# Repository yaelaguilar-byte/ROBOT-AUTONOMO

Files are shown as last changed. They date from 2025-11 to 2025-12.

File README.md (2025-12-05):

Introduction and description of the project: This project is a proposal for an Autonomous Robot, developed from modifications made to a radio-controlled (RC) car chassis obtained from a content creator known as ""Duke Doks" through his YouTube channel and his official website:

https://dukedoks.com/portfolio/guia-chasis-rc/

The same document contains the download link for the .STL files for 3D printing.
It was decided to use this chassis for 3D printing instead of modifying a model ordered online because the latter option presented greater design and control limitations, which could have led to complications and greater limitations when making modifications to the chassis. In contrast, using a chassis as a base and then selecting the other components and materials needed for the car's proper functioning would have been preferable. Throughout this project, several aspects had to be covered in addition to the selection and modification of the aforementioned chassis, which are:
- Mobility Management
- Power and Sensory Management
- Obstacle Management

The first point refers to the choice and origin of the chassis selected for the car; that is, whether it is purchased, printed, or made completely from scratch. In our case, we have already mentioned where the selected chassis model came from and the reasons for our choice, which can be summarized as greater design control, decision-making, and, in short, a wider range of possibilities and freedom to modify and test with other components not considered in the original design. For example, changing the motor controller of an RC car ESC to a power H-bridge.

The second part of the project focuses on how the robot had to perform its most basic functions, specifically forward movement, reverse movement, and steering. For the forward and reverse motion, we selected a 21T 540 brushed motor because it provides enough torque to drive a gear system located at the rear of the robot. This gear system is connected to a shared axle for the two rear wheels, allowing the robot to move forward and backward through rear-wheel drive powered by the motor. To ensure proper operation of the traction motor, we implemented a BTS7960 H-bridge to control its direction. This was necessary because the brushed motor requires a high current, making it incompatible with more delicate H-bridges, such as the commonly used L298N. Regarding steering, we decided to use an MG996R high-torque servo motor. This choice was made because the MG996R features metal gears, providing greater durability compared to more common models like the SG90. The SG90, with its internal plastic gears, is more prone to stripping and therefore unsuitable for this project. In contrast, the MG996R offers the robustness needed for reliable steering. Finally, the HC-SR04 ultrasonic sensors implemented in the robot provide directional awareness. These sensors are responsible for sending and receiving signals to detect nearby objects, allowing both the servo motor and the traction motor to react accordingly.

Lastly, the third point refers to the algorithm designed and implemented for the robot. This algorithm is explained in detail in the files included in this repository, where you can find the flowchart, the pseudocode, and the final C code written for the Arduino UNO (which was the microcontroller chosen for this project). Below is a summary of how the algorithm works: Once the robot and all its electronics are powered through a LiPo battery and a voltage regulator, the system waits for an input signal—specifically, a push button connected to one of the Arduino pins. When the push button is pressed, the robot enters the void loop() and begins executing the main program. The first step is sending a signal to the H-bridge to rotate the motor clockwise, allowing the robot to move forward. During operation, two HC-SR04 ultrasonic sensors placed on the left and right sides of the robot continuously detect whether there is an object near either side. Based on this detection, the servo motor adjusts its steering direction away from the closest wall or obstacle to keep the robot moving forward safely. Additionally, a third ultrasonic sensor is mounted at the front of the robot. Its purpose is to detect obstacles directly ahead. If an obstacle is detected, the sensor sends a signal to the Arduino, which then commands the H-bridge to reverse the motor’s direction from clockwise to counterclockwise. This causes the robot to move backward for a short moment, allowing it to avoid the detected obstacle.

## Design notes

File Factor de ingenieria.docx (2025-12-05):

Factor de ingenieria

Factor de ingenieria

Para la base de este proyecto que fue la planificación, tuvimos primero que revisar los detalles que hacían referencia a las características que debía cumplir el robot según la convocatoria para la competencia, es por eso que desde el principio tuvimos que tener bien en consideración el diseño del Chasis, ya que sería la parte más fundamental del robot y que determinaría aspectos clave como lo son el espacio total que teníamos para los componentes y el circuito de funcionamiento de nuestro robot, es por eso que

no sabíamos si modificar un carro RC, diseñarlo o imprimir un modelo CAD, pero después de analizarlo un poco más a detalle, nuestra elección final fue imprimir un modelo CAD para carro de radiocontrol (RC) qué encontramos en un canal de YouTube llamado “Duke Doks”, la principal razón de esta elección era que teníamos un mayor control en el aspecto técnico y funcional del robot, al poder elegir con muchas mayor libertad los componentes y materiales que usamos para el proyecto, cosa que resultó ser un completo acierto en contraposición a si hubiéramos comprado y modificado un Chasis por aparte, ya que si hubiéramos elegido esta última opción, habríamos tenido que enfrentar problemas como lo podrían haber sido una elección más restringida de componentes y un menor control de diseño para nuestro robot, es por eso que imprimimos en 3D el diseño CAD qué previamente se mencionó, con el detalle de que se tuvo que modificar ya que no cumplía con las medidas permitidas establecidas en el reglamento. También trabajamos sobre este chasis añadiéndole un servomotor MG996R, una Arduino UNO, un motor Brushed 540, un puente h BTS7690, un regulador de voltaje LM2596 y tres sensores ultrasónicos HC-SR04 con soportes para cada uno.

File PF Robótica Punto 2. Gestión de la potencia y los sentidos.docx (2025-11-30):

Gestión de la potencia y los sentidos

Primeramente, para este proyecto se decidió usar como fuente de alimentación una batería LiPo, los valores de alimentación de esta misma de esta misma, los cuales son:

- Voltaje: Número de celdas

- Amperaje: Cantidad de corriente que se puede extraer de la batería en ua hora antes de que quedar vacía

- Cantidad de C: Potencia total que puede entregar la batería

Y gracias a este abanico tan amplio de posibilidades, tuvimos varias opciones para usar como fuente de alimentación, sin embargo, al final nos decidimos por usar una batería LiPo Gen Ace de 2 celdas (7.4V) a 1000mAh y 45C.

Gracias a las cualidades de esta batería, nuestro carrito contaba con una potencia más que suficiente para llevar a cabo todas sus funciones perfectamente, esto gracias a que la corriente máxima que puede entregar la batería es de aproximadamente 45 A, valor obtenido de calcular este mismo con la formula:

- Corriente máxima = (C)*(mAh/1000)

Por lo que nuestro calculo sería el siguiente:

- Corriente máxima = (45)*(1000/1000) = 45 A

Por lo que sabemos que nuestra batería puede entregar hasta un máximo de 45 Amperes, y dados los componentes que usamos:

- Arduino: 0.10 A
- Sensores (3): 0.045 A
- Servo (moviendo): 1.0 A
- Motor 540 + Driver BTS7960 (trabajo): 7.0 A

Donde el Arduino brinda la lógica de programación, los sensores las lecturas para la dirección del carrito, el servo se encarga de darle la dirección con base a la información que recibe de los sensores, y el motor mas el driver/Puente H sirven para brindarle el movimiento de avance y retroceso al robot. Haciendo un cálculo de la cantidad de corriente aproximada que consume cada uno, nos daría un aproximado de 8.145 A en total, lo que nos comprueba que la batería que empleamos es perfecta para alimentar todos nuestros componentes.

Los sensores que se usaron para este proyecto fueron los ultrasónicos HC-SR04 esto gracias a que, si bien son sensores mas caros que, por ejemplo, los infrarrojos o de color, son capaces de arrojar unas lecturas más “Limpias” en comparación con estos 2 últimos, principalmente en lugares abiertos con mucha luz o a distancias un poco mas largas, aun así, durante las pruebas del robot, se encontraron complicaciones al tratar con este modelo de sensor en específico, las principales fueron que a veces presentaban lecturas fantasma (Ruido) que generaban un movimiento errático en el servomotor, razón por la que se empleo un capacitor de 4700 microfaradios a 35V para suavizar un poco las lecturas, además de esto, los sensores resultaron ser bastante sensibles y faciles de descalibrar al momento de ser usados por el robot mismo, lo que llevo a que en varios ocasiones se quemaran y/o dañaran por problemas como el ruido o las lecturas fantasma, y fue por esta misma razón que los sensores se tuvieron que cambiar un total de 4 veces. Son por estas y mas razones que en un punto se consideró cambiar a sensores mismamente ultrasónicos, pero de modelo VL53L0X, pero por falta de tiempo, no se pudieron implementar en el proyecto, aun así, estos se tomaran en cuenta en un futuro si se quisiesen hacer correcciones al carrito.

La gestión de la potencia y la dirección es sencilla, el algoritmo para el funcionamiento del motor es sencillo:
Consiste que en al iniciarse el programa, y presionar un pushbotton, el Arduino empezara a mandar y leer lecturas de los 3 sensores ultrasónicos con los que cuenta el carrito, al mismo tiempo que mandara señales PWM al puente H BTS7960 para que haga girar el motor brushed 540 en sentido horario, y permita el avance total del robot gracias a su tracción trasera, ahora bien, del tema de la dirección como tal, se encargan el servomotor MG996R y los 3 sensores ultrasónicos HC-SR04, lo que hará el Arduino será evaluar y comparar la lecturas del sensor frontal/delantero para medir constantemente si hay un obstáculo enfrente del carrito, si lo hay, entonces el Arduino mandara una señal al puente H para que invierta el sentido de la señal PWM, es decir, lo que hará será invertir la dirección a la que girara el motor brushed, cambiando su sentido de horario a antihorario para que el robot pueda ir en reversa y de estar manera evitar el obstáculo que tiene enfrente, ahora bien, en caso de que el sensor delantero no detecte un obstáculo visible, entonces el motor seguirá girando en sentido horario, a la par, los 2 sensores laterales (Izquierdo y derecho) estarán enviando señales constantemente para medir las distancias de los obstáculos en los costados, teniendo de esta manera una referencia de distancia para cada lado, estas mismas referencias serán enviadas y comparadas por el Arduino, quien hará una diferencia con estos mismos valores para calcular aproximadamente en que lado esta mas cerca en obstáculo, lo cual se determinara si el resultado de la diferencia (resta) es positivo o negativo, según sea el valor, será el lado contrario a la lectura menor la que se tomara como referencia para establecer si hay un obstáculo mas próximo que el lado opuesto, por lo que ya con esta información, simplemente el Arduino hará una corrección en el ángulo del servomotor, para de esta manera calcular una varianza bastante aproximada que se tendrá que realizar a los ángulos predefinidos de la dirección del motor (Izquierda, derecha, centro) para de esta manera, poder otorgarle la dirección al carro gracias al sistema Ackermann que se implemento y se manipulado por el servomotor de torque MG996R, y gracias a que la cantidad de corriente que proporciona la batería es más que suficiente para alimentar toda la lógica de control (Arduino, sensores y puente H) y potencia (Motor 540 brushed y servomotor MG996R al tener un torque más grande) que nuestro carrito cuenta con los elementos suficiente para dar un buen resultado ya una vez eliminado el ruido eléctrico gracias al capacitor que se le añadió para unas lecturas y funcionamiento más limpio.

Diagrama de conexiones elaborado en Fritzing:

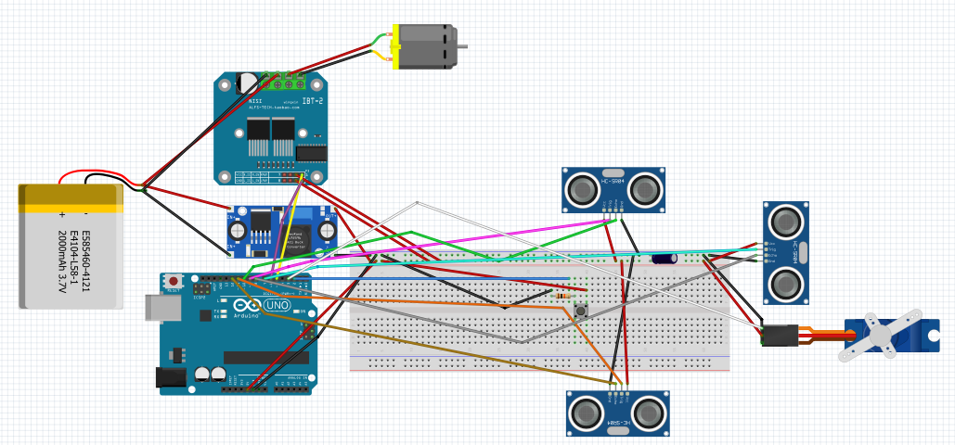
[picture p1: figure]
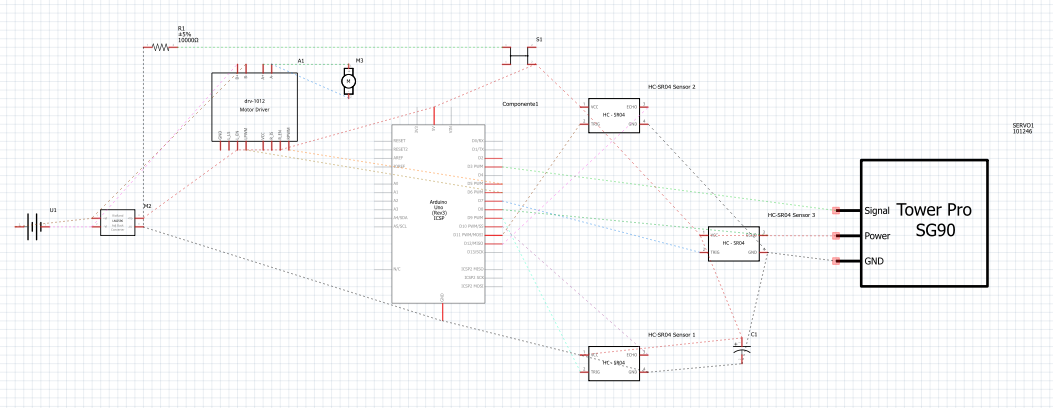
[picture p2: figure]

(A falta de un servomotor MG996R y un motor brushed 540, se decidió usar los que se encuentran disponibles en el simulador)

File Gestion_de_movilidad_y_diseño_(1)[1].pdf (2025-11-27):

# Gestión de movilidad y diseño

## Diseño

Para el chasis elegimos usar el modelo de un carro RC que encontramos en internet el cual se tuvo que modificar ya que no cumplía con las medidas establecidas en el reglamento. Es importante mencionar que como es un modelo sacado de internet ocupa componentes especiales para armarlo, los cuales pudimos comprar en una aplicación de compras en línea.

Para que el carro avance se eligió un motor de escobillas RC brusher modelo 540 de 27T, el cual ofrece un buen balance entre torque y velocidad, esenciales en el diseño de nuestro carro. El motor se implementa a partir de un sistema de engranajes para proporcionar el movimiento a un eje compartido por las 2 llantas traseras de tal modo que ambas llantas giren al mismo tiempo, teniendo así el carro una tracción trasera.

Para que el carro pudiera girar usando un solo un motor, tomamos la decisión de implementar un sistema Ackermann en la parte delantera que es dirigido con un servomotor MG996R controlado por un Arduino UNO.

En el apartado de los sensores, elegimos usar unos sensores ultra sónicos HC-SR04 los cuales elegimos por cuestiones de practicidad.

Para el micro controlador elegimos usar un Arduino UNO ya que se adapta a nuestras necesidades y ya contábamos con el.

## Gestión de movimientos

El carro cuenta con 4 movimientos, hacia delante, hacia atrás, hacia la izquierda y hacia la derecha, los dos primeros movimientos se llevan a cabo gracias a un motor brusher 540 posicionado en la parte trasera el cual es controlado mediante un puente h driver BTS7960, la finalidad este motor es únicamente proporcionar movilidad a las llantas traseras, el motor está conectado a un sistema de engranajes que permiten que ambas llantas giren ya que están conectadas mediante un eje compartido. Los movimientos tres y cuatro son posibles gracias a un sistema Ackermann (comúnmente usado en la industria automotriz) el cual está conectado a las dos llantas delanteras y es dirigido por un servomotor MG996R que se encarga de darle las direcciones.

Para que el carro pueda hacer cualquiera de estos movimientos está equipado con tres sensores ultra sónicos HC-SR04 los cuales están posicionados en la parte delantera y a los costados del robot, estos sensores se encargan de mandar señales al micro controlador (el cual es un Arduino UNO) que se encarga de gestionar los movimientos del carro, funcionan de tal manera que si el sensor que está posicionado en la parte de delantera detecta algo a cierta distancia, el carro se para y retrocede, seguido a eso los sensores frontales empiezan a censar y el que detecte una distancia más cercana a la pared mandará una señal al servomotor para dirigirse en dirección contraria.

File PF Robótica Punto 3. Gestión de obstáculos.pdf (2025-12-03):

# Gestión de obstáculos

## Lógica de programación

Nuestro robot autónomo está programado para para evitar chocar con obstáculos, nuestra lógica de programación es que en un principio el robot permanezca apagado hasta la activación mediante un push button, seguido a eso el carro empieza a avanzar y el servomotor se posiciona en un ángulo de 90° hasta que el sensor frontal detecte algún obstáculo a una cierta distancia, una vez el sensor haya detectado un obstáculo el motor se detiene y retrocede durante 0.75 segundos y seguido a eso se vuelve a parar, cuando el motor se para los sensores colocados al costado del carro empiezan a censar y el que detecte un obstáculo a menor distancia mandará una señal al servomotor para que gire en dirección contraria y así evitar chocar.

Pseudocódigo:

1.-Inicio

2.-Condicion: ¿Botón presionado? /¿Hay lectura "LOW" del pushbutton asociado al pin 3?
--- No: Esperar hasta que la condición se cumpla
--- Si: Avanzar con el programa

3.-Enviar señal PWM al pin L del puente H y hacer girar el motor en sentido horario para avanzar

4.-Leer valores de los sensores laterales y frontal

5.-Condicion: ¿La distancia (El valor) del sensor delantero es MENOR que distancia de choque?
--- Si: Imprimir un valor giro de 80 grados al servomotor y enviar señal PWM al pin R del puente H y hacer girar el motor en sentido antihorario para retroceder, luego esperar 0.75 segundos y regresar al paso 3
--- No: Comparar distancia de los 2 sensores laterales y aplicar una resta para saber de qué lado hay un objeto más cerca, para de esta manera hacer una corrección al multiplicar el resultado de la resta por la constante "K" (Cuyo valor es 1.2) para hacer una corrección del ángulo del servomotor, luego se vuelve a comparar: ------- Si el valor del nuevo ángulo es mayor que el valor máximo del servo (Que vale 115 grados), entonces el valor del ángulo corregido pasa a ser el valor máximo del servo
------- Si el valor del nuevo ángulo es menor que el valor mínimo del servo (Que vale 55 grados), entonces el valor del ángulo corregido pasa a ser el valor mínimo del servo

--- Luego se imprime el valor del nuevo ángulo para el servomotor y se siguen enviando señales PWM al pin L al puente H para que haga girar el motor en sentido horario y avanzar

6.-Se retorna a la condición 4

Diagrama de flujo:

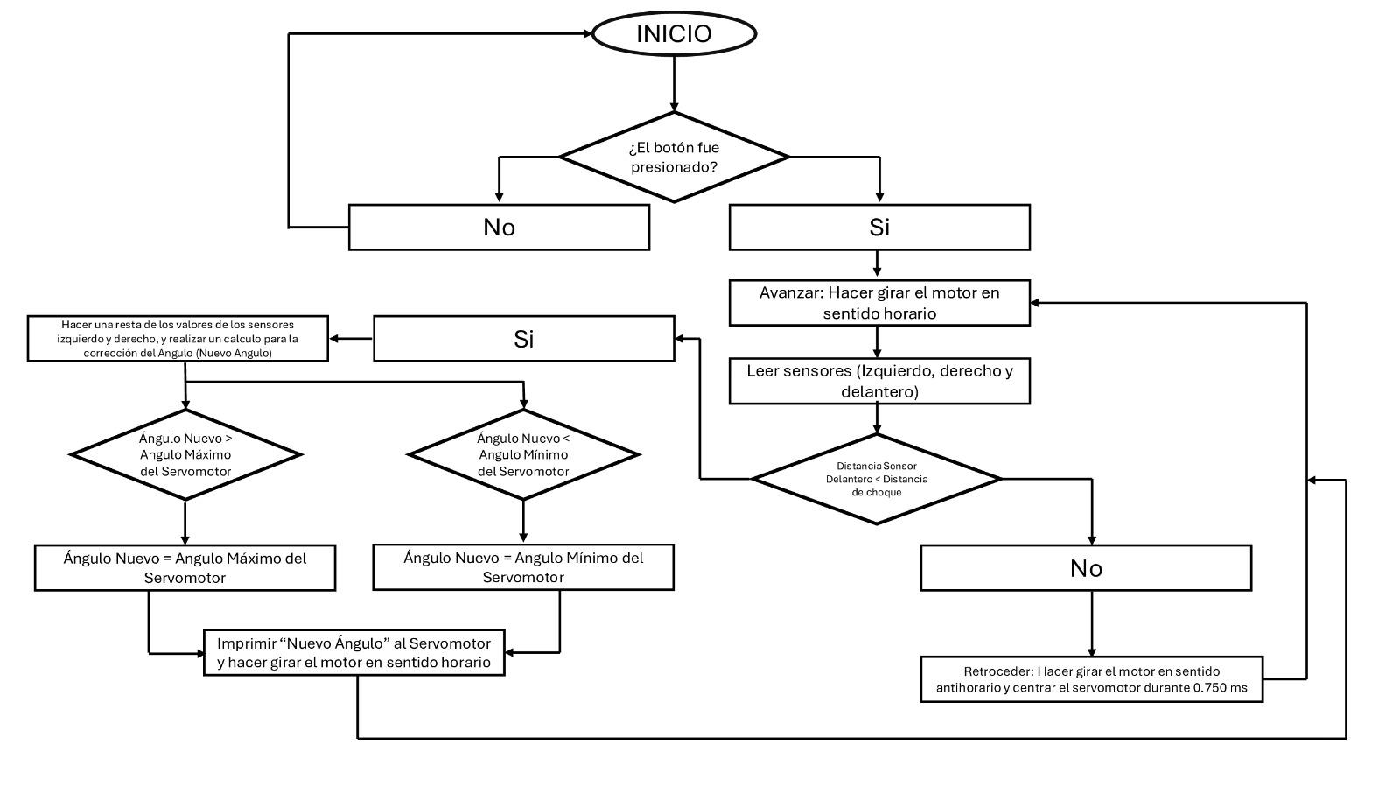
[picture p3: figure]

Implementación del pseudocódigo (Algoritmo) en código: #include <Servo.h>

// --- 1. DEFINICIÓN DE PINES ---

// Servomotor MG996R (Dirección) Servo direccionServo;
const int SERVO_PIN = 3;

// Driver BTS7960 (Propulsión) const int MOTOR_PWM_L = 6; const int MOTOR_PWM_R = 5;

// Sensores Ultrasónicos HC-SR04 const int TRIG_L = 9;
const int ECHO_L = 10;

const int TRIG_R = 11;
const int ECHO_R = 12;

const int TRIG_D = 7;
const int ECHO_D = 8;

// Botón con pull-down en el pin 2
const int BUTTON_PIN = 2;

// --- VARIABLE PARA ACTIVAR EL ROBOT ---bool robotActivo = false;

// --- 2. CONSTANTES DE CALIBRACIÓN ---

const float Kp = 1.2;

const int SERVO_CENTRO = 80; const int SERVO_LIMITE_MAX = 115; const int SERVO_LIMITE_MIN = 55;

const int velocidad = 30;
const int retroceso = 60;

const float DISTANCIA_CHOQUE = 25.0; const int TIEMPO_REVERSA = 250;

// --- 3. FUNCIONES ---

float leerDistancia(int trigPin, int echoPin) { digitalWrite(trigPin, LOW); delayMicroseconds(2);
digitalWrite(trigPin, HIGH); delayMicroseconds(10);
digitalWrite(trigPin, LOW);

long duracion = pulseIn(echoPin, HIGH); float distancia = duracion * 0.034 / 2;

if (distancia > 200 || distancia < 0) return 200; return distancia;
}

void avanzar(int velocidad) { analogWrite(MOTOR_PWM_L, velocidad); analogWrite(MOTOR_PWM_R, 0);
}

void detener() {
analogWrite(MOTOR_PWM_L, 0); analogWrite(MOTOR_PWM_R, 0); }

void retrocederMotor(int velocidad) { analogWrite(MOTOR_PWM_L, 0); analogWrite(MOTOR_PWM_R, retroceso); }

// --- 4. SETUP ---

void setup() {
delay(2000);

pinMode(TRIG_L, OUTPUT); pinMode(ECHO_L, INPUT); pinMode(TRIG_R, OUTPUT); pinMode(ECHO_R, INPUT); pinMode(TRIG_D, OUTPUT); pinMode(ECHO_D, INPUT);

pinMode(MOTOR_PWM_L, OUTPUT); pinMode(MOTOR_PWM_R, OUTPUT);

direccionServo.attach(SERVO_PIN); direccionServo.write(SERVO_CENTRO); detener();

Serial.begin(9600);

// --- CONFIGURACIÓN DEL BOTÓN (PULL-DOWN REAL) ---pinMode(BUTTON_PIN, INPUT);

Serial.println("Robot Listo. Presiona el botón para iniciar...");

// Espera hasta que el botón sea presionado
while (digitalRead(BUTTON_PIN) == LOW) {
delay(20);
}

Serial.println("Boton presionado. Robot ACTIVADO."); robotActivo = true;
}

// --- 5. LOOP PRINCIPAL ---

void loop() {

// Si aún no se ha activado el robot, no hace nada if (!robotActivo) {
return;
}

// ---- LECTURA DE SENSORES ----
float dist_delantera = leerDistancia(TRIG_D, ECHO_D); float dist_izquierda = leerDistancia(TRIG_L, ECHO_L); float dist_derecha = leerDistancia(TRIG_R, ECHO_R);

// --- EVITACIÓN FRONTAL ---
if (dist_delantera < DISTANCIA_CHOQUE) {

detener();
delay(TIEMPO_REVERSA);

direccionServo.write(SERVO_CENTRO); retrocederMotor(velocidad);
delay(750);

detener();
}

// --- CONTROL PROPORCIONAL LATERAL ---else {

float error = dist_derecha - dist_izquierda;
int correccion = (int)(error * Kp);

int nuevo_angulo = SERVO_CENTRO + correccion;

if (nuevo_angulo > SERVO_LIMITE_MAX) nuevo_angulo = SERVO_LIMITE_MAX;
if (nuevo_angulo < SERVO_LIMITE_MIN) nuevo_angulo = SERVO_LIMITE_MIN;

direccionServo.write(nuevo_angulo);
avanzar(velocidad);
}

// ---- DEBUG SERIAL (Opcional) ----Serial.print("DI: "); Serial.print(dist_izquierda);

Serial.print(" | DD: "); Serial.print(dist_derecha);
Serial.print(" | DF: "); Serial.print(dist_delantera);
Serial.print(" | Angulo: "); Serial.println(direccionServo.read());

delay(50);
}

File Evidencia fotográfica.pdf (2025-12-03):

## Evidencia fotográfica

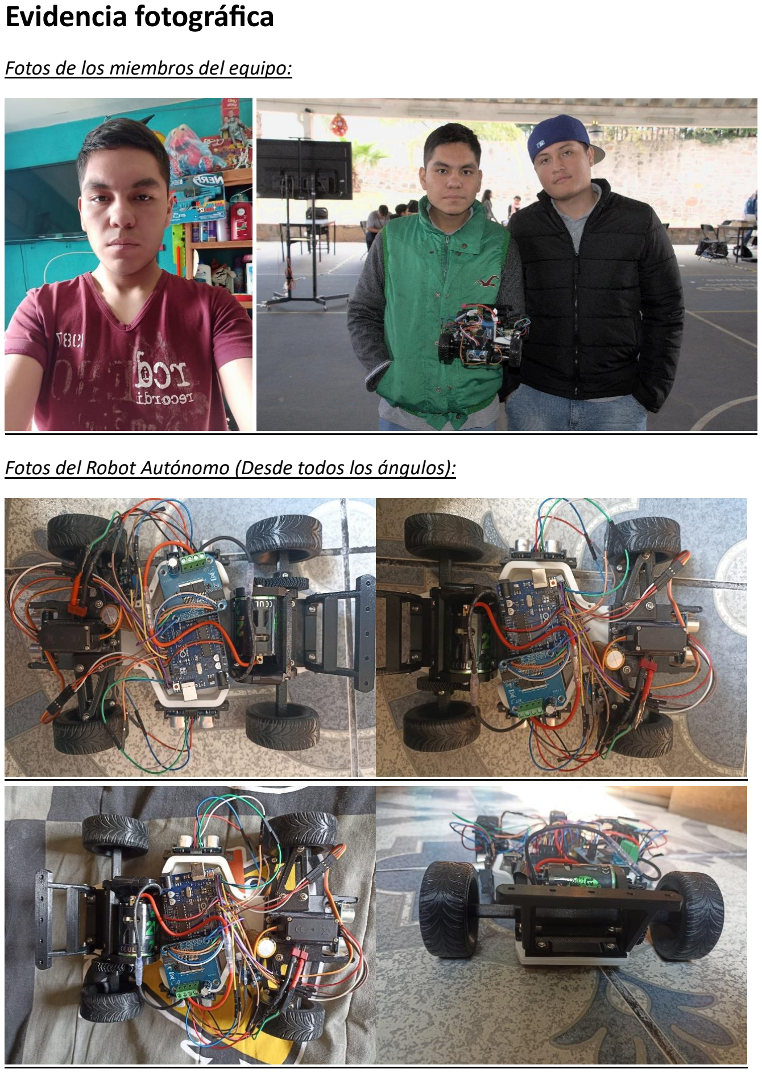
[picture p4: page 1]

Fotos de los miembros del equipo:

Fotos del Robot Autónomo (Desde todos los ángulos):

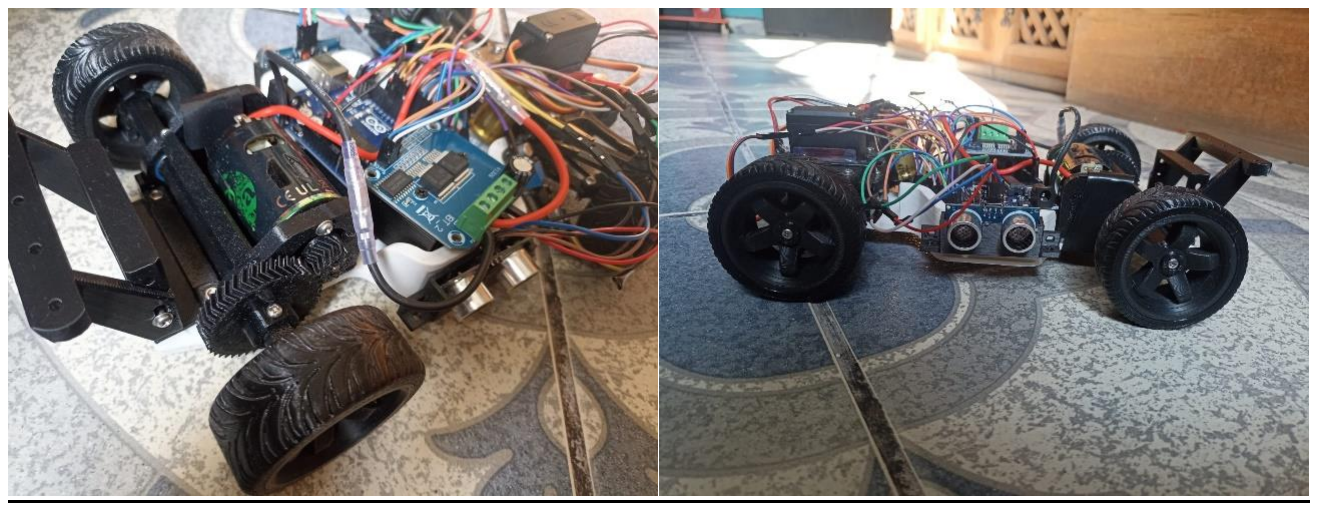
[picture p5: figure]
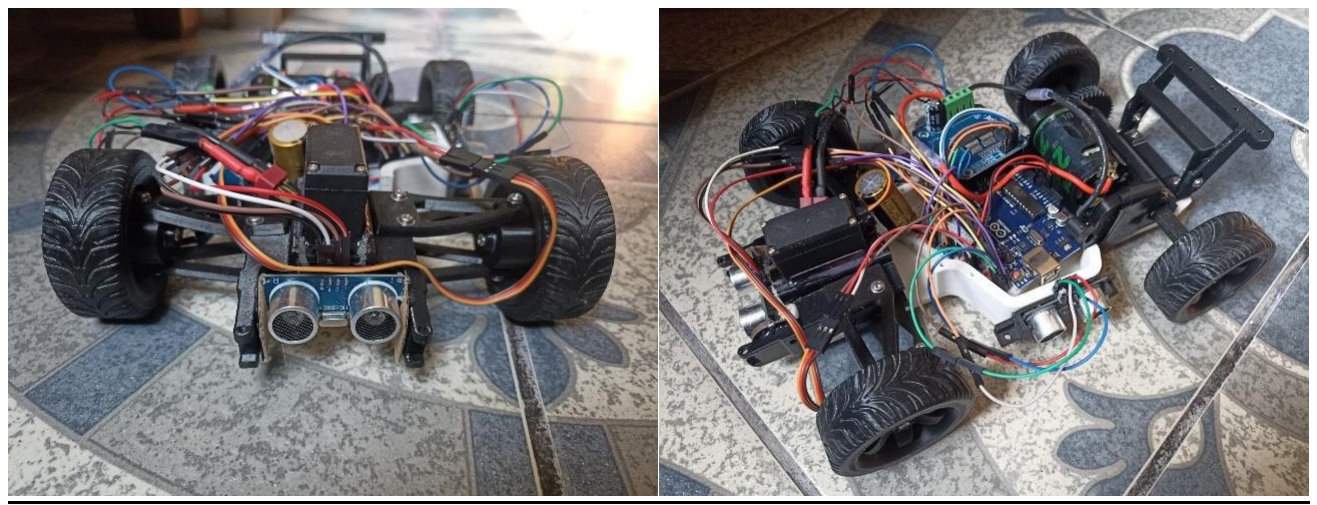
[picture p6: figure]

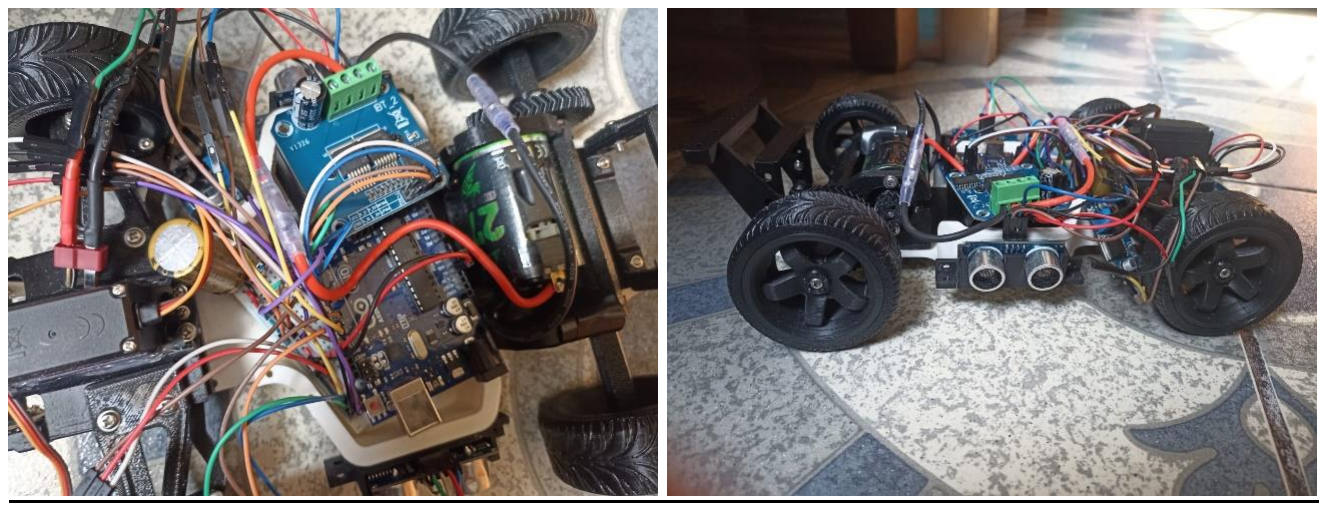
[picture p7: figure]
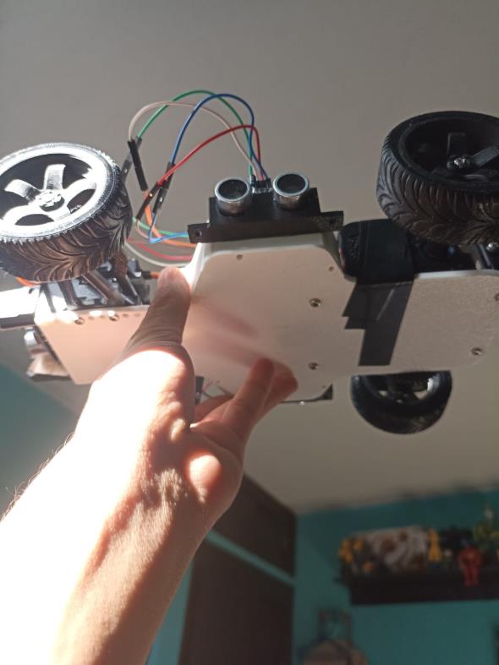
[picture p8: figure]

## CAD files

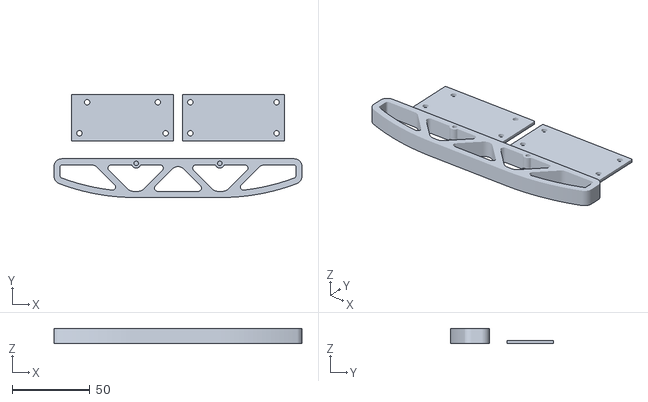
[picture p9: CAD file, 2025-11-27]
print_05-dks_basic_dukedoks_rear-absorbers-bumper.stl
160.0 x 66.5 x 9.90

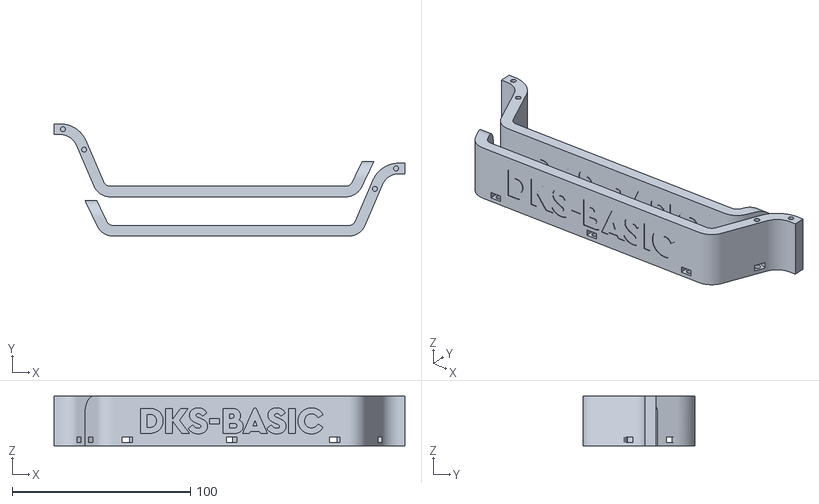
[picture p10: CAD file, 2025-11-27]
print_02-dks_basic_dukedoks_chassis-2.stl
197.0 x 63.0 x 28.0

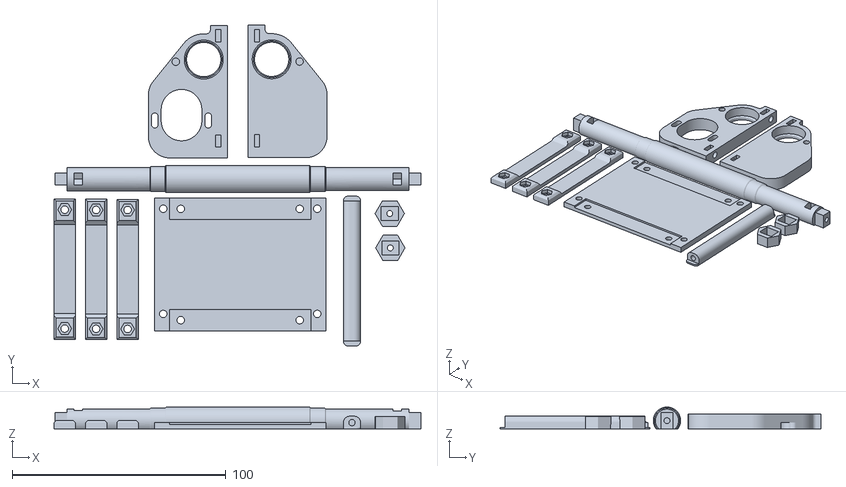
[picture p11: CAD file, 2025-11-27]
print_03-dks_basic_dukedoks_rear-axis.stl
171.6 x 150.0 x 10.3

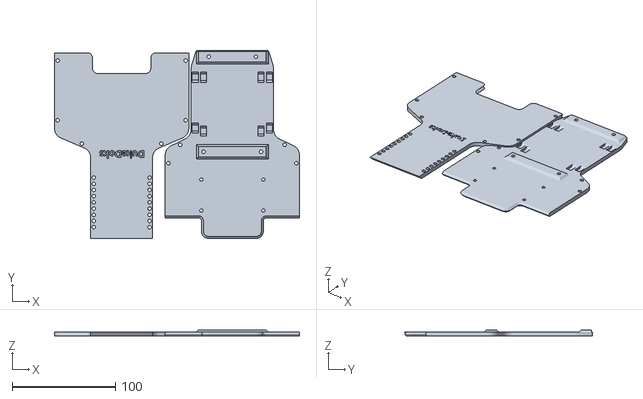
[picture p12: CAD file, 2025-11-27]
print_01-dks_basic_dukedoks_chassis-1_a.stl
237.1 x 182.1 x 6.00

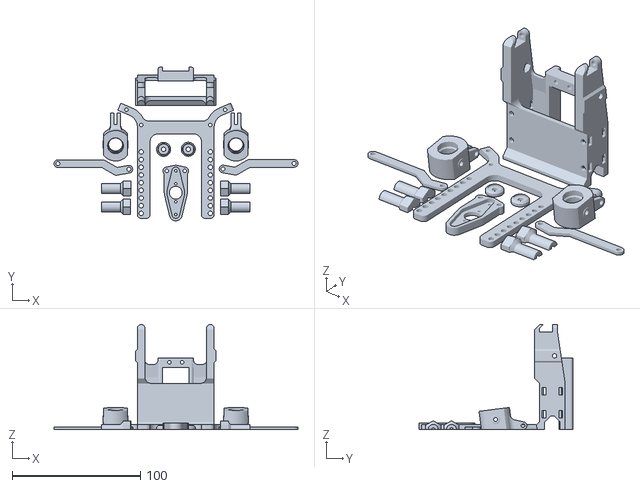
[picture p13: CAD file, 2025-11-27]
print_04-dks_basic_dukedoks_stearing.stl
190.5 x 120.1 x 82.0

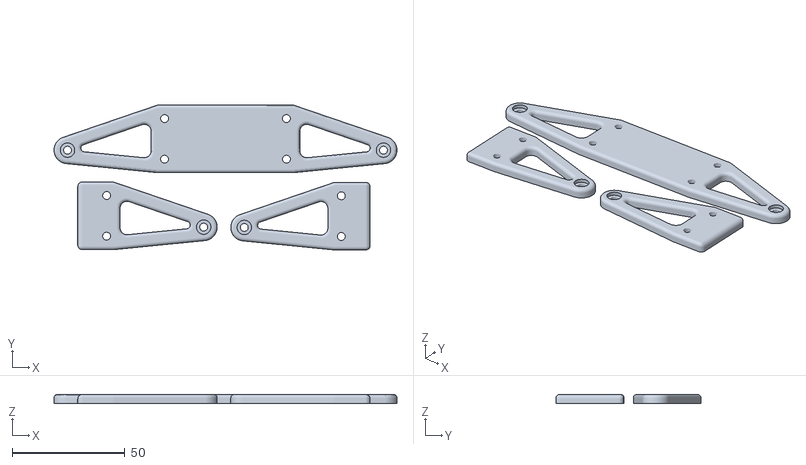
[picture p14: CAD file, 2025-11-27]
print_06-dks_basic_dukedoks_front-absorbers.stl
152.0 x 64.2 x 4.00

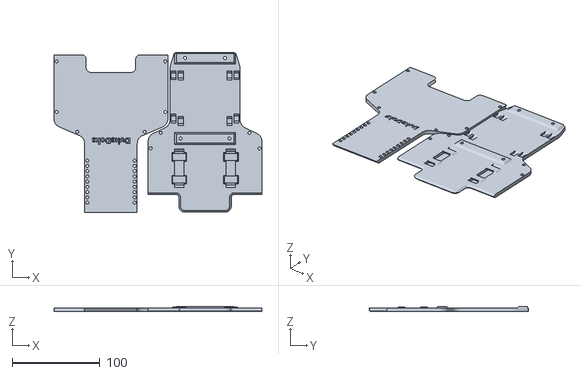
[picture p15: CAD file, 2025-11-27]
print_01-dks_basic_dukedoks_chassis-1_b.stl
237.4 x 182.2 x 6.00

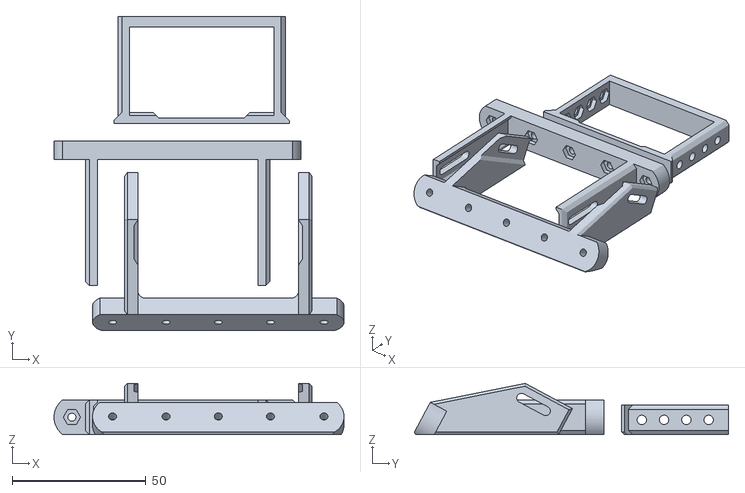
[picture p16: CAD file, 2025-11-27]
print_08-dks_basic_dukedoks_case-holders.stl
108.4 x 117.5 x 19.1

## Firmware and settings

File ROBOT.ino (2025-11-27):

#include <Servo.h>

// --- 1. DEFINICIÓN DE PINES ---

// Servomotor MG996R (Dirección)
Servo direccionServo;
const int SERVO_PIN = 3;

// Driver BTS7960 (Propulsión)
// Ambos pines se usarán como PWM para controlar la velocidad (RPM)
// El L_EN y R_EN están cableados a VCC (HIGH) por el hardware.
const int MOTOR_PWM_L = 6; // Pin RPM 
const int MOTOR_PWM_R = 5; // Pin RPM 

// Sensores Ultrasónicos HC-SR04
// Izquierda
const int TRIG_L = 9;
const int ECHO_L = 10;
// Derecha
const int TRIG_R = 11;
const int ECHO_R = 12;
// Delantero
const int TRIG_D = 7;
const int ECHO_D = 8;

// --- 2. CONSTANTES DE CALIBRACIÓN (AJUSTAR EN PRUEBAS) ---

// Control Proporcional
const float Kp = 1.2;         // Ganancia Proporcional (Ajustar: 1.0 a 2.0)

// Servo
const int SERVO_CENTRO = 85;  // Nuevo centro ligeramente ajustado de 90 a 85 grados
const int SERVO_LIMITE_MAX = 130; // Ángulo máximo de giro (Izquierda)
const int SERVO_LIMITE_MIN = 40;  // Ángulo mínimo de giro (Derecha)

// Motor y Velocidad
const int velocidad = 110; // Velocidad de avance (0-255)

// Evitación de Obstáculos
const float DISTANCIA_CHOQUE = 15.0; // Distancia límite en cm para detener el robot
const int TIEMPO_REVERSA = 250;      // Tiempo en ms que retrocede el robot

// --- 3. FUNCIONES DE UTILIDAD ---

// Función para leer la distancia de un sensor HC-SR04
float leerDistancia(int trigPin, int echoPin) {
    // Limpiar el pin TRIG
    digitalWrite(trigPin, LOW);
    delayMicroseconds(2);
    // Enviar pulso de 10µs
    digitalWrite(trigPin, HIGH);
    delayMicroseconds(10);
    digitalWrite(trigPin, LOW);

    // Leer el pulso de retorno
    long duracion = pulseIn(echoPin, HIGH);
    // Convertir a distancia (cm) 
    // Velocidad del sonido (340 m/s o 0.034 cm/µs). Distancia = (Duración * 0.034) / 2
    float distancia = duracion * 0.034 / 2;
    
    // Opcional: limitar para ignorar lecturas demasiado lejanas
    if (distancia > 200 || distancia < 0) {
        return 200; 
    }
    return distancia;
}

// Función para mover el motor hacia adelante
void avanzar(int velocidad) {
    // En el BTS7960, para avanzar, enviamos la misma señal PWM a ambos RPM
    // ya que el L_EN/R_EN están en VCC y la lógica interna ya está manejada.
    analogWrite(MOTOR_PWM_L, velocidad); 
    analogWrite(MOTOR_PWM_R, 0);
}

// Función para detener el motor (frenado)
void detener() {
    analogWrite(MOTOR_PWM_L, 0); 
    analogWrite(MOTOR_PWM_R, 0);
}

// Función para mover el motor hacia atrás (usando la lógica de H-bridge del BTS7960)
// Esto dependerá de cómo conectaste los pines, ajusta si es necesario.
// Si ambos PWM giran al mismo tiempo, el motor se detiene (como en 'detener')
// Para el 540 necesitas invertir la polaridad, lo cual se hace con los pines de control que 
// tu no estás usando (L_EN/R_EN cableados a VCC).
// Por simplicidad, y dado tu cableado, usaremos solo 'detener' y dependeremos de la lógica de giro.

// --- 4. CONFIGURACIÓN INICIAL ---

void setup() {
    // Configuración de pines de sensores
    delay(2000);
    pinMode(TRIG_L, OUTPUT); pinMode(ECHO_L, INPUT);
    pinMode(TRIG_R, OUTPUT); pinMode(ECHO_R, INPUT);
    pinMode(TRIG_D, OUTPUT); pinMode(ECHO_D, INPUT);
    
    // Configuración de pines de motor
    pinMode(MOTOR_PWM_L, OUTPUT);
    pinMode(MOTOR_PWM_R, OUTPUT);
    
    // Inicialización del servomotor
    direccionServo.attach(SERVO_PIN);
    direccionServo.write(SERVO_CENTRO); // Centrar el servo al inicio
    detener(); // Detener el motor
    
    // Serial para debug (Opcional)
    Serial.begin(9600);
}

// --- 5. BUCLE PRINCIPAL DE NAVEGACIÓN ---

void loop() {
    // a. LECTURA DE SENSORES
    float dist_delantera = leerDistancia(TRIG_D, ECHO_D);
    float dist_izquierda = leerDistancia(TRIG_L, ECHO_L);
    float dist_derecha = leerDistancia(TRIG_R, ECHO_R);

    // --- LÓGICA DE DETECCIÓN FRONTAL (Prioridad Máxima) ---
    if (dist_delantera < DISTANCIA_CHOQUE) {
        // 1. DETENER
        detener();
        // 2. RETROCEDER (Esta función asume que tu cableado permite reversa, si no, solo DETENER)
        // Para simplificar, si no estás usando los pines de dirección, solo frenamos y esperamos.
        // Si no puedes retroceder, el robot quedará atascado. 
        // Si tu driver tiene pines de dirección (ej. DIR_A y DIR_B), DEBERÍAS USARLOS para el 540.
        delay(TIEMPO_REVERSA); 
        
        // 3. GIRAR LA DIRECCIÓN al máximo opuesto para reorientarse (ej. 45 grados a la izquierda si el último giro fue a la derecha)
        // Por defecto, giramos ligeramente a la derecha para intentar salir.
        direccionServo.write(SERVO_LIMITE_MAX); // Intenta girar bruscamente a la izquierda
        avanzar(velocidad/2); 
        delay(500); // Espera medio segundo para que el robot se mueva un poco
        detener();
    }
    
    // --- LÓGICA DE CONTROL LATERAL PROPORCIONAL ---
    else {
        // Error: Si Error > 0, el robot está cerca del muro derecho (DD es menor que DI). Necesita girar IZQUIERDA (ángulo > SERVO_CENTRO)
        // Si Error < 0, el robot está cerca del muro izquierdo (DI es menor que DD). Necesita girar DERECHA (ángulo < SERVO_CENTRO)
        float error = dist_derecha - dist_izquierda; 
        
        // Cálculo de la corrección
        int correccion = (int)(error * Kp);
        
        // Nuevo ángulo de dirección
        int nuevo_angulo = SERVO_CENTRO + correccion;
        
        // Aplicar límites
        if (nuevo_angulo > SERVO_LIMITE_MAX) nuevo_angulo = SERVO_LIMITE_MAX;
        if (nuevo_angulo < SERVO_LIMITE_MIN) nuevo_angulo = SERVO_LIMITE_MIN;
        
        // Ejecutar el movimiento
        direccionServo.write(nuevo_angulo);
        avanzar(velocidad);
    }

    // --- LÓGICA DE DEBUG (Opcional, activa el Serial Monitor) ---
    Serial.print("DI: "); Serial.print(dist_izquierda);
    Serial.print(" | DD: "); Serial.print(dist_derecha);
    Serial.print(" | DF: "); Serial.print(dist_delantera);
    Serial.print(" | Angulo: "); Serial.println(direccionServo.read());
    
    delay(50); // Pequeño retardo para estabilidad de lectura/escritura (ajustar)
}

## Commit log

2025-11-27 Add files via upload
    Archivios stl de chasis
    [print_01-dks_basic_dukedoks_chassis-1_a.stl, print_01-dks_basic_dukedoks_chassis-1_b.stl, print_02-dks_basic_dukedoks_chassis-2.stl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]
2025-12-02 Add files via upload
    Código de Robot Autónomo ACTUALIZADO
